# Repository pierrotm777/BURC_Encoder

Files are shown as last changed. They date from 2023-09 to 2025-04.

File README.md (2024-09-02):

# BURC_Encoder
 Universal RC Box System.  
 
 The BURC modules use the RCUL protocol by Rc-Navy.
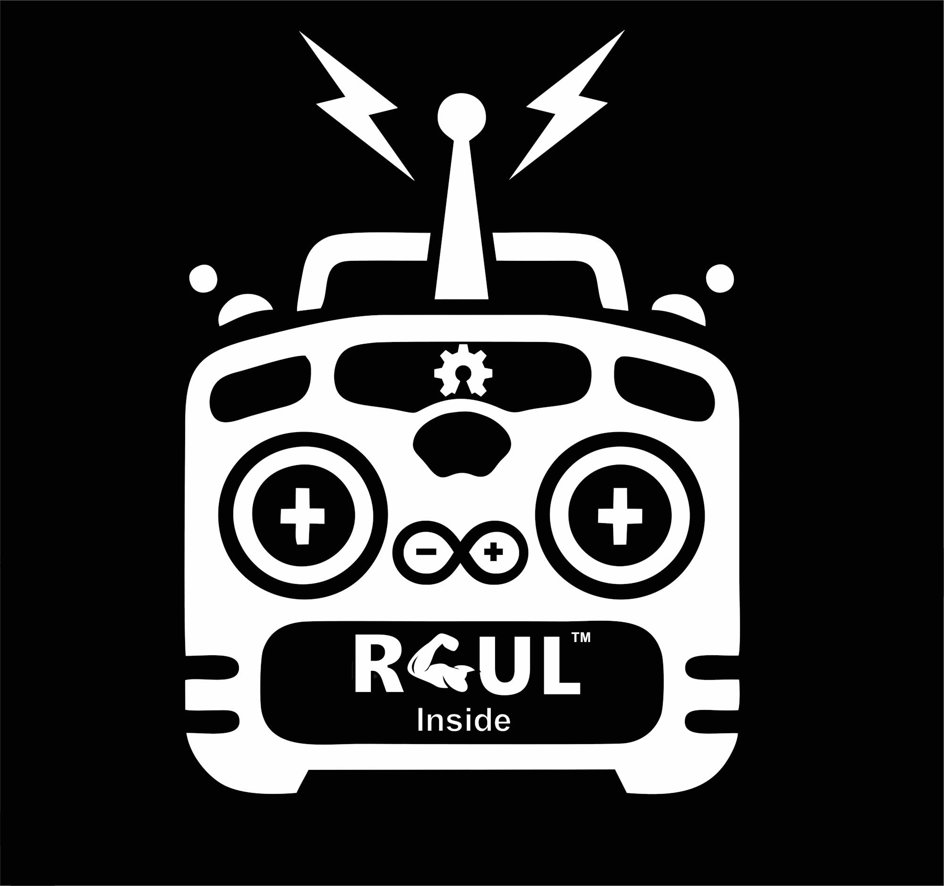
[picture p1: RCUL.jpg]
RCUL
   

## Rc-Navy
The BURC system is build by Philippe Loussouarn ([Rc-Navy](http://p.loussouarn.free.fr/index.html)). 

## Presentation of the BURC system
[What's BURC](https://p-loussouarn-free-fr.translate.goog/arduino/exemple/RCUL/RCUL.html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)

## Compatibles modules usable with BURC
All these modules behind
- [Ms8 v2](https://github.com/Ingwie/OpenAVRc_Hw/tree/V3/MutltiSwitch_Sw8_V2)  
- [Ms16](https://github.com/Ingwie/OpenAVRc_Hw/tree/V3/MultiSwitch_Sw16-ProMicro)  
- [Sound&SmokeModule](https://github.com/Ingwie/OpenAVRc_Hw/tree/V3/Sound%26SmokeModule)  
- [Xany2Msx](https://github.com/Ingwie/OpenAVRc_Hw/tree/V3/Xany2Msx/Firmware_Msx)  
- [Xany2Misc](https://github.com/Ingwie/OpenAVRc_Hw/tree/V3/Xany2Msx/Firmware_Misc)  
- Hall sensor:  
  * [Hall I2C sensor](https://github.com/Ingwie/OpenAVRc_Hw/tree/V3/Capteur_Hall_I2C)  
  * [Hall I2C sensor mini](https://github.com/Ingwie/OpenAVRc_Hw/tree/V3/Capteur_Hall_I2C_Mini)  
- [MultiSwitch_MosFet](https://github.com/Ingwie/OpenAVRc_Hw/tree/V3/MultiSwitch_MosFet)  
- [Ms8 Pulseq](https://github.com/Ingwie/OpenAVRc_Hw/tree/V3/PulseSeq) 
- [Servo 360°]() 

## Build BURC
### Schematic  
Encoder:  
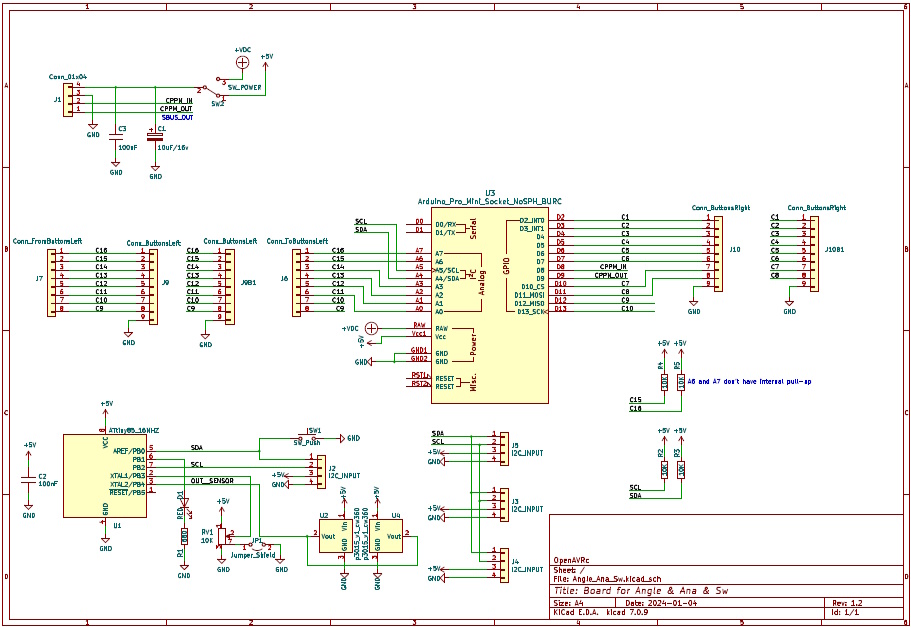
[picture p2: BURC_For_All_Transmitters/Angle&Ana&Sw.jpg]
Encoder
  
16 switchs by I2C bus:  
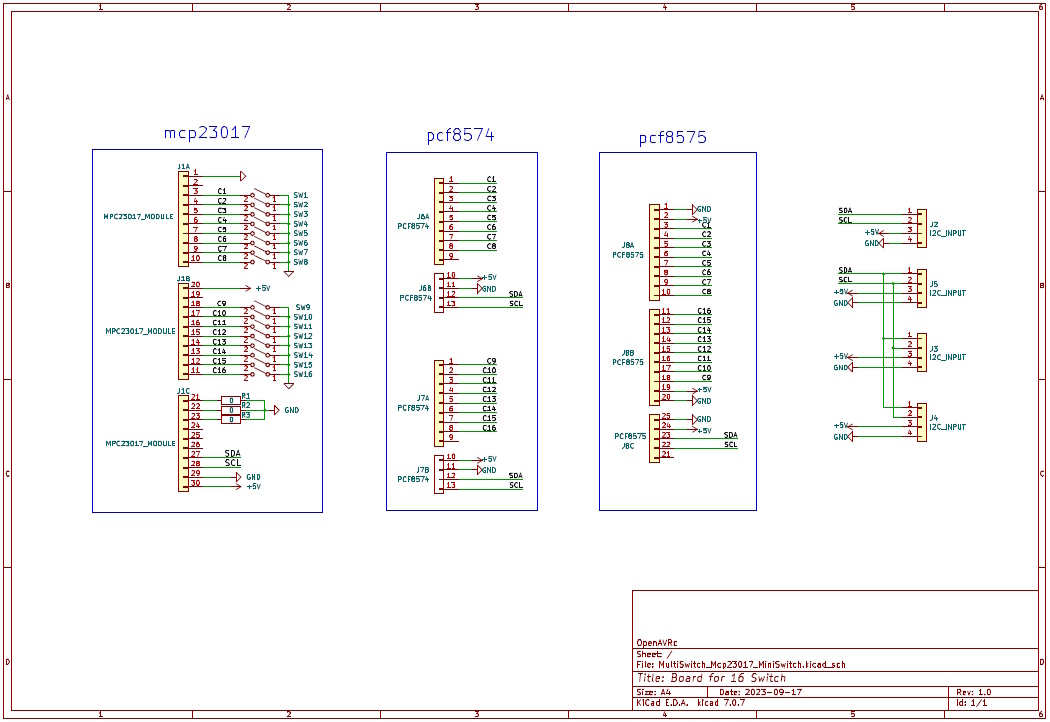
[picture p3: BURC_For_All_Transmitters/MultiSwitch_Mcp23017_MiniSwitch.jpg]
  
16 switchs on Arduino:  
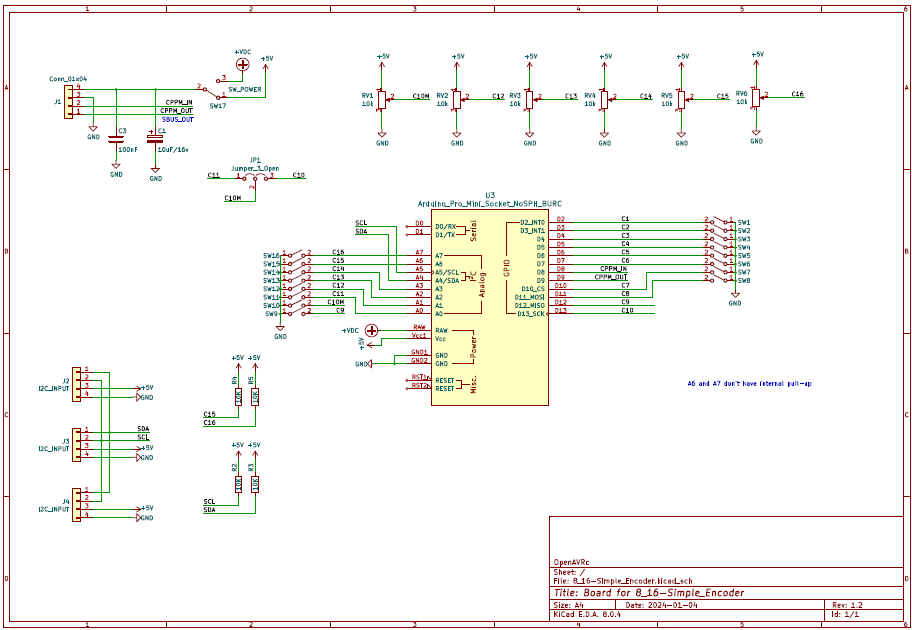
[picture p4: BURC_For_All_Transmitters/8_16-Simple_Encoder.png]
 

### Boards  
Two cards make up the BURC system.
The BURC Encoder is connected to the transmitter over a **CPPM** input or a **SBUS** input.
- The BURC Encoder:
  * Encoder board (include 8 switchs, 1 360° hall sensor and 1 slider, need one proportional channel) 
  Can command up to 128 fonctions (8x16) by exemple 8 Ms16 modules, use 1 channel for each 16 switchs module.  

  <table border="2">
  <tr>
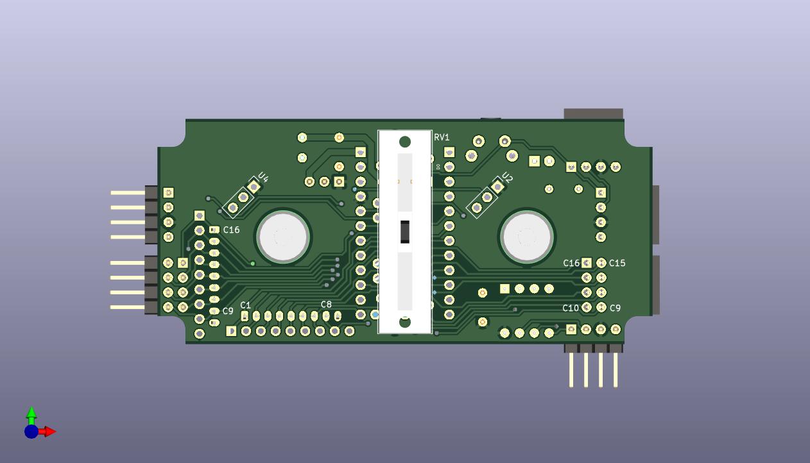
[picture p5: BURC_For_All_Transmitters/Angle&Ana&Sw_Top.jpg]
  <td></td>
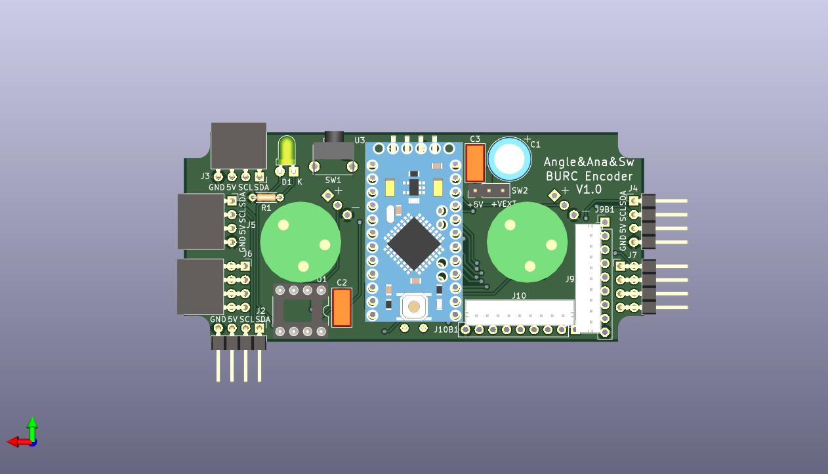
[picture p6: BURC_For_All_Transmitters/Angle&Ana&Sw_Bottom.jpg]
  <td></td>
  </tr>
  </table>
  
  The hall sensor command a Schottel motor type by rotation, and the slider command the motor's power.  
  This board is the **main board** system and can command **several 16 switchs** board.  
  The interface between all the boards use an **I2C** bus.  

  The same board can be used for the left or right motor, and assume to wire only one of the two hall sensor an the 8 first switchs.  
  The second board will command the 8 other switchs and the second slider (No need another arduino Pro Mini in the second circuit board) .  
  An Attiny85 receive these orders from the first board and command the second hall sensor and the second slider.  
  A dashboard exemple for two motors:  
  <table border="2">
  <tr>
  <td></td>
  </tr>
  </table>
    
  * Encoder symplified board (include 16 switchs or 8 switchs and 6 potentiometers, need one proportional channel) 
  Can command up to 128 fonctions (8x16) by exemple 8 Ms16 modules, use 1 channel for each 16 switchs module.  

  <table border="2">
  <tr>
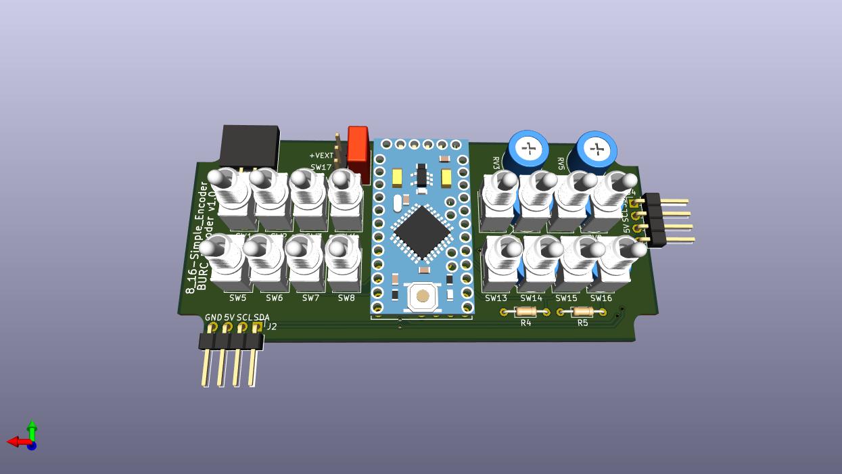
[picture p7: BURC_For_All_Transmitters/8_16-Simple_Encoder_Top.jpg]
  <td></td>
  </tr>
  </table>
  
  You need to remove the resistor's LED on pin D13 (C10 signal).  
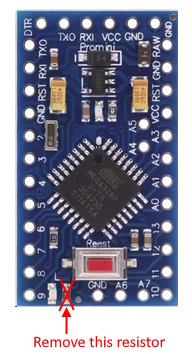
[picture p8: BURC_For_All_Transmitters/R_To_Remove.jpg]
R to remove
    

- The Switch board:

  16 Switchs board (need one proportional channel) 
  Each switch can command 1 fonction.  
  The type of command depend of the [Ms8](https://github.com/Ingwie/OpenAVRc_Hw/blob/V3/MutltiSwitch_Sw8_V2/MS8-Xany-V2_Manuel_Utilisateur.pdf)/[Ms16](https://github.com/Ingwie/OpenAVRc_Hw/blob/V3/MultiSwitch_Sw16-ProMicro/MS16-Xany_Manuel_Utilisateur.pdf) possibilities.    
  This board read 16 switchs by 1 MCP23017 or 2 PCF8574 or 1 PCF8575.
  <table border="2">
  <tr>
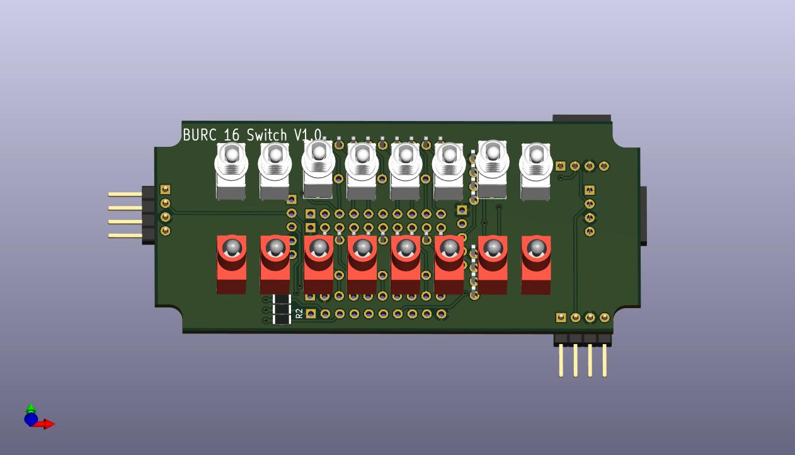
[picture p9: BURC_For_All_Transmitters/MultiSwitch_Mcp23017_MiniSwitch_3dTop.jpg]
  <td></td>
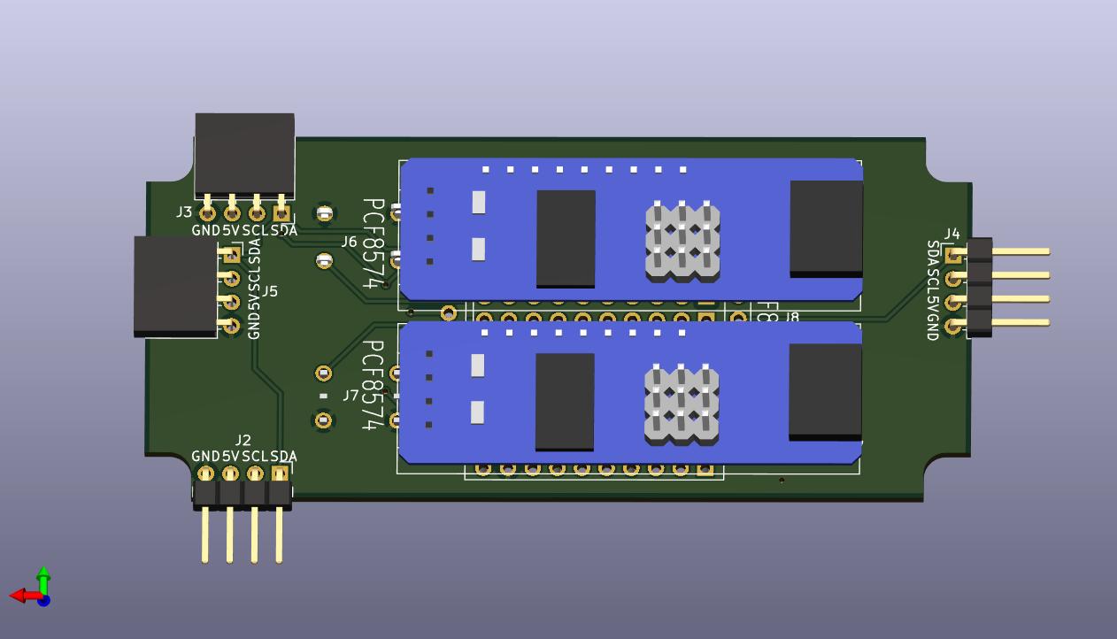
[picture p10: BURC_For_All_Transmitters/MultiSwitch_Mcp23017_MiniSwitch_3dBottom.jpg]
  <td></td>
  </tr>
  </table>  
  
  A main board coupled to  a second board and 2 16 switchs boards:
  <table border="2">
  <tr>
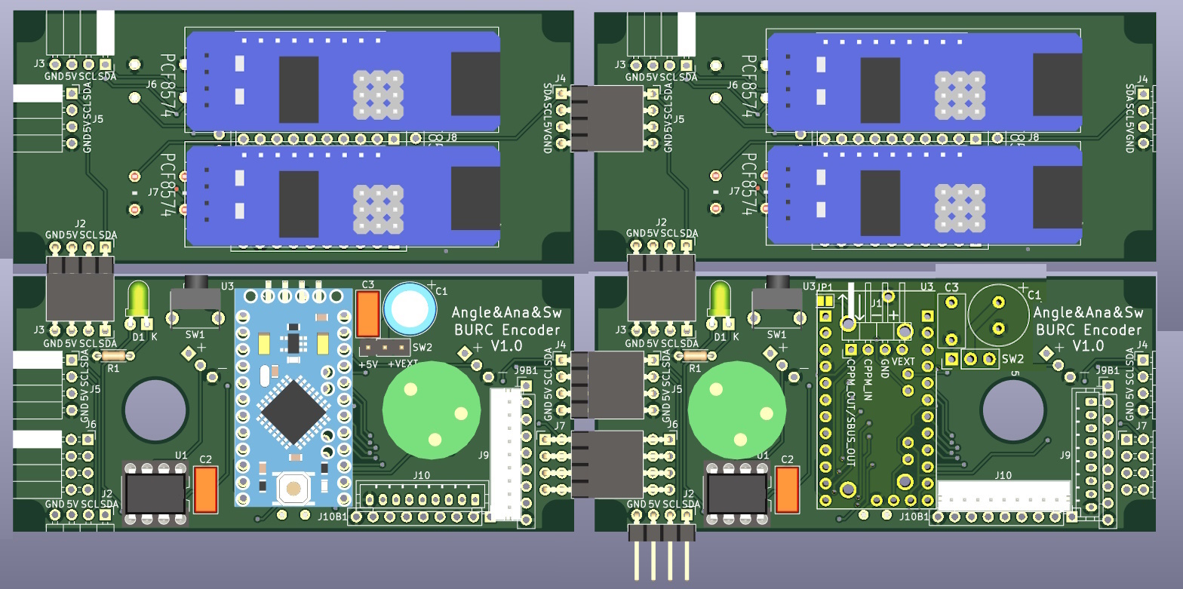
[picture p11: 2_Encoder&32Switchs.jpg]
  <td></td>
  </tr>
  </table>  
  
  A main board and a 48 switchs coupled:
  <table border="2">
  <tr>
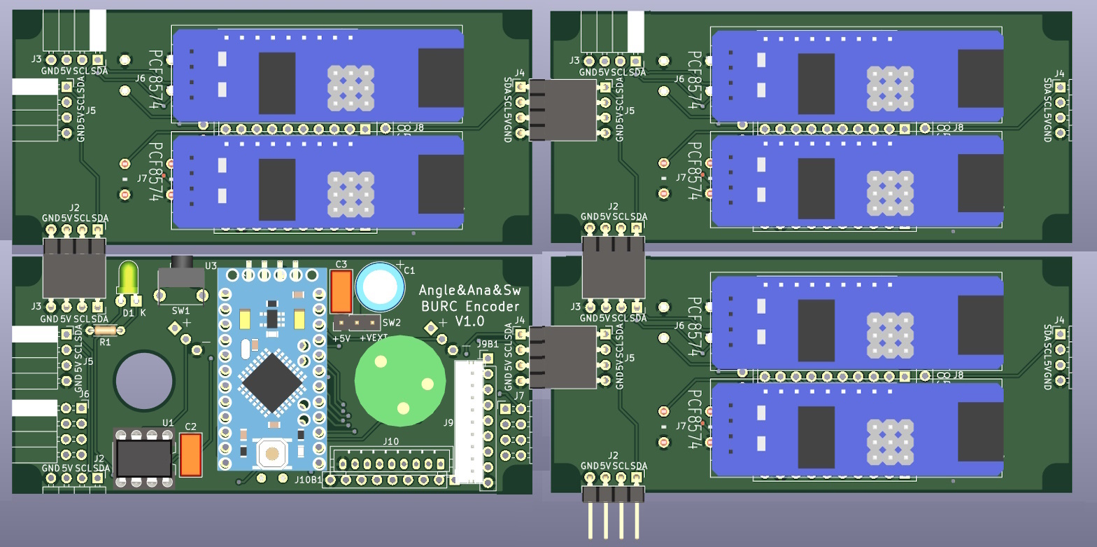
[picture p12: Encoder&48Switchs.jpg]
  <td></td>
  </tr>
  </table>  

### Firmware upload for Pro Mini
- Windows:  
The best method is to use [Xloader](https://github.com/pierrotm777/BURC_Encoder/blob/main/PROG/Windows/XLoader.zip).  
The last firmware is the version [v0.14](https://github.com/pierrotm777/BURC_Encoder/blob/main/PROG/Windows/BURC_CODER_V0_14.hex).  

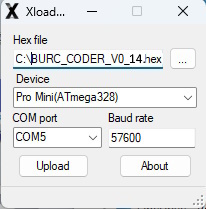
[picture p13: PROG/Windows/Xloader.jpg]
Xloader
  

- Other Os:
Use you Arduino IDE for find witch command to use.
In my case, the command is :  
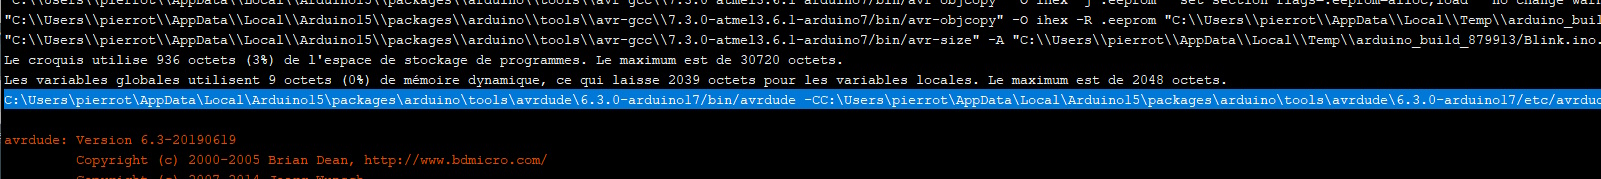
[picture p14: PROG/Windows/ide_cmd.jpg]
  
  * replace the hex file path C:\Users\pierrot\AppData\Local\Temp\arduino_build_879913/Blink.ino.hex by your firmware path.  
  * create a script file with this change.  

### Firmware upload for Attiny85
  * use an USBAsp programmer and [ARDUDESS Gui](https://github.com/ZakKemble/AVRDUDESS/releases/) or an [Arduino Uno board](https://www.instructables.com/Programming-ATtinys-Micro-Controllers-With-Arduino)
  * define the fuses (for 16Mhz internal mode), low=0xF1, high=0xDF, extended=0xFF
  * last firmware is the version [v2.2](https://github.com/pierrotm777/BURC_Encoder/blob/main/PROG/Windows/HallAna2A1335_V2_2.hex).  

### Exemple BURC build
- You will find [here](https://cults3d.com/fr/mod%C3%A8le-3d/jeu/burc-pad) an exemple of 3d files by **croky_b** witch accept all the BURC's boards.  

## Configure the BURC Encoder
  * Pro Mini:
    * Connect a FTDI interface to the Arduino Pro Mini and your PC.
    * Use a terminal for send your commands.
    * Set your terminal with 115200 bauds, 8 bits, no parity, 1 bit stop and CR or CRLF (see LIGNE.TERM).
    * Type ENTER key for see the module's version.

  * Attiny85 (360° encoder) A push button allows:
    * calibrating the analog sensor (min and max): before powering the ATtiny85, press the Push button and hold it for  1 - 2 seconds.
    * setting the I2C address: before powering the ATtiny85, press the Push button and hold it for more than 4 seconds.  
      Additionally, it can read an analogic input (0/5V)

## Settings usables
The list of messages that can be transported in each RCUL instance is:  
- SW1-SW8:   the state of 8 contacts of the 8 contacts of an 8 I/O I/O extender or a 16 I/O extender or the first 8 contacts of the 16 native contacts of the Arduino
- SW9-SW16:  the state of the last 8 contacts of a 16 I/O extender or the last 8 contacts of the 16 native contacts of the Arduino
- SW1-SW16:  the state of 16 contacts of a 16 I/O extender or of the 16 native contacts of the Arduino
- ANGLE:     the value of the angle of a 360° angle sensor
- ANGLE+ANA: the value of the angle of a 360° angular sensor + an analog value  

On the encoder there are 16 native contacts from C1 to C16.  
Among C8 to C16, 6 are also analog inputs which correspond to pins C11 to C16.  
So C11 to C16 are also ANA1 to ANA6 (these are my names, not the names of the "arduino" pins):  
We therefore have 6 analog channels at our disposal (just as we wire a pot there instead of an switch or push button).  

We can make extended RCUL messages of the type:  
**RCUL1.MESSAGE=C1-C8@0x00+ANA1** (which will transmit 8 contact states + an 8-bit ana value:  
You obviously have to wire a knob to pin C11).  
**RCUL2.MESSAGE=C9-C16@0x24+ANA2** (which will transmit 16 contact states + an 8-bit ana value:  
You obviously have to wire a knob to pin C12).  

So, with **RCUL1.MESSAGE=C1-C8@0x00+ANA1** or **RCUL2.MESSAGE=C9-C16@0x24+ANA2**,  
for an MS8 (V1 or V2), you can control the 8 outputs + the additional proportional output.  
You can also order the Sound&Smoke module which uses the 8 contacts to launch 8  
different sounds and the ana value to adjust the volume of the DF Player from the transmitter.  

We can also do:
**RCUL3.MESSAGE=C1-C16@0x25+ANA3** (which will transmit 16 contact states + an 8-bit analog value:  
You obviously have to wire a knob to pin C12)
So, with **RCUL3.MESSAGE=C1-C16@0x25+ANA3** for an MS16, you can control the 16 outputs + the additional proportional output.  

So, if we want to use the first 8 contacts C1 to C8 of your 16-input I2C extender at address 0x24,  
we just have to create another RCUL instance in which we refer to the first 8 contacts: **RCUL5.MESSAGE=C1-C8@0x24**
And with RCUL5 we can, for example, order another MS8.
So we will have the first 8 contacts of the I2C extender with 16 inputs (at address 0x24) used by RCUL5 to control an MS8 (for example) 
and the last 8 contacts of the 16-input I2C extender (at address 0x24) used by RCUL2 (which also uses ANA2) to control a Sound&Smoke.

It is possible to directly map an analog value (ANA1 to AN6), inverted or not, to a channel.  
To do this, you must use the command **RCULx.MESSAGE=RC.ANA[_INV]y** with x=RCUL instance number and y is the ANA channel number (from 1 to 6):  
Example: **RCUL4.MESSAGE=RC.ANA_INV1**  
A simple solution for build a little 6 channels hanset WITH BURC features.  

Debug method:  
To test an RCUL channel in CPPM, we loop pin8 back to pin9 and we do an **RX.MODE=RCUL4@CPPM4** and after an **RX.DBG=1** command.  

## I2C Devices address
<pre>
PCF8574         <b>0x20 to 0x23</b>  
MCP23017        <b>0x24 to 0x27</b>  
PCF8574A        <b>0x38 to 0x3B</b> (very difficult to find)  
PCF8575         <b>0x24 to 0x27</b>  
PCF8575A        <b>0x3C to 0x3F</b> (very difficult to find)  
ANGLE SENSOR    <b>0x0C to 0x0F</b>  
</pre>

Exemple of configuration:
```
CONF?
LANG=FR
LIGNE.TERM=CRLF
ECOLAGE.MODE=CPPM_OUT
CPPM.MODU=NEG
CPPM.ENTETE=300
CPPM.VOIE.NB=8
CPPM.PERIODE=22500
RCUL.REPET=2
RCUL1.VOIE=5
RCUL1.MESSAGE=ANGLE+ANA@0x0C
RCUL1.TEST=OFF
RCUL2.VOIE=6
RCUL2.MESSAGE=C9-C16@0x24
RCUL2.TEST=OFF
RCUL3.VOIE=8
RCUL3.MESSAGE=C1-C8@0x24+ANA1
RCUL3.TEST=OFF
RCUL4.VOIE=7
RCUL4.MESSAGE=RC.ANA_INV1
RCUL4.TEST=OFF
RCUL5.VOIE=OFF
RCUL5.MESSAGE=C1-C8@0x00
RCUL5.TEST=OFF
RCUL6.VOIE=OFF
RCUL6.MESSAGE=C1-C8@0x00
RCUL6.TEST=OFF
RX.MODE=RCUL6@CPPM6
RX.DBG=0
```

<pre>
- LANG=FR                       define language (FR or UK)  
- LIGNE.TERM=CRLF               define terminal return (CR or CRLF)  
- ECOLAGE.MODE=CPPM_OUT         CPPM_OUT+CPPM_IN/CPPM_OUT/SBUS_OUT;FUTABA[_INV] Defines the transmitter training mode
- CPPM.MODU=NEG                 CPPM signal is build with negative pulses (POS is possible)  
- CPPM.ENTETE=300               300 first width CPPM pulse  
- CPPM.VOIE.NB=8                CPPM build 8 channels  
- CPPM.PERIODE=22500            CPPM periode in mS
- SBUS.SPEED=NORMAL				NORMAL/FAST Defines the SBUS speed (NORMAL=14ms, FAST=7ms)  
- RCUL.REPET=2                  the encoder repeats the same thing twice for a better transmission result  
- RCUL1.MESSAGE=ANGLE+ANA@0x0C  for command an azimutal motor (direction and motor)  
- RCUL2.MESSAGE=C9-C16@0x24     8 buttons on MCP23017 (address 0x24)  
- RCUL3.MESSAGE=C1-C8@0x24+ANA1 8 buttons on MCP23017 and analog button (module Sound&Smoke for 8 sounds et volume)
- RCUL4.MESSAGE=RC.ANA_INV2     1 analogique channel inverted  
</pre>

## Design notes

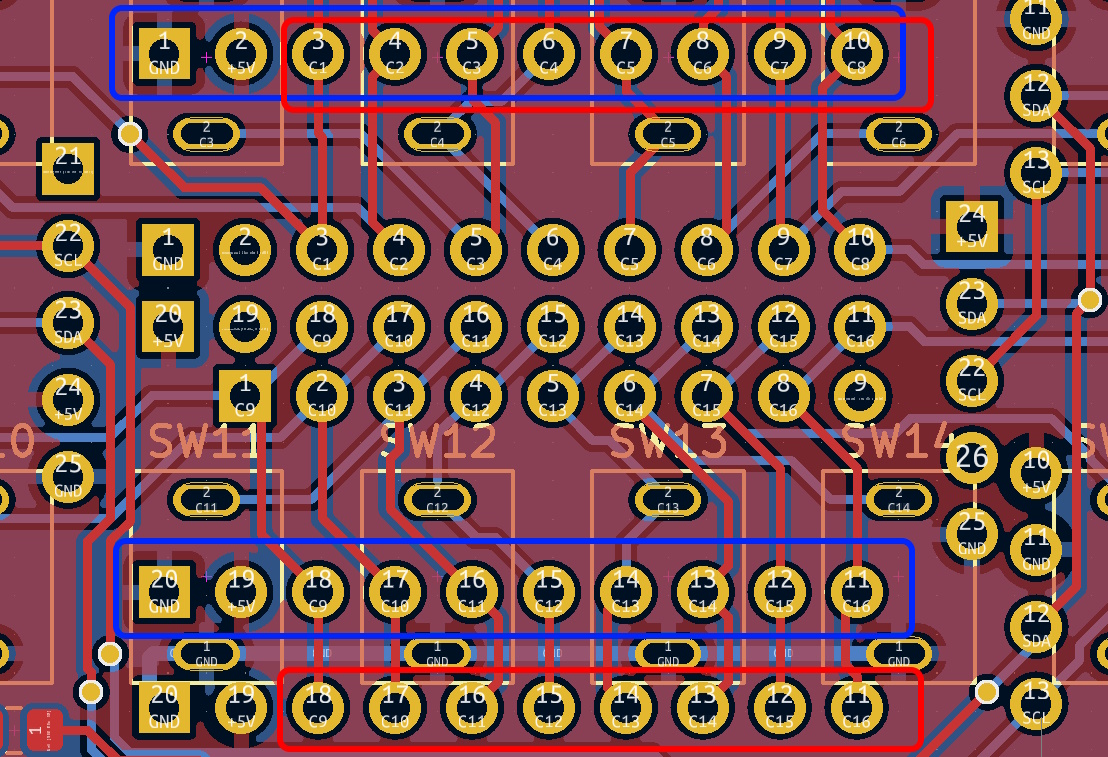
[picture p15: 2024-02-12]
BURC_For_All_Transmitters/PCF8575_pinout.jpg

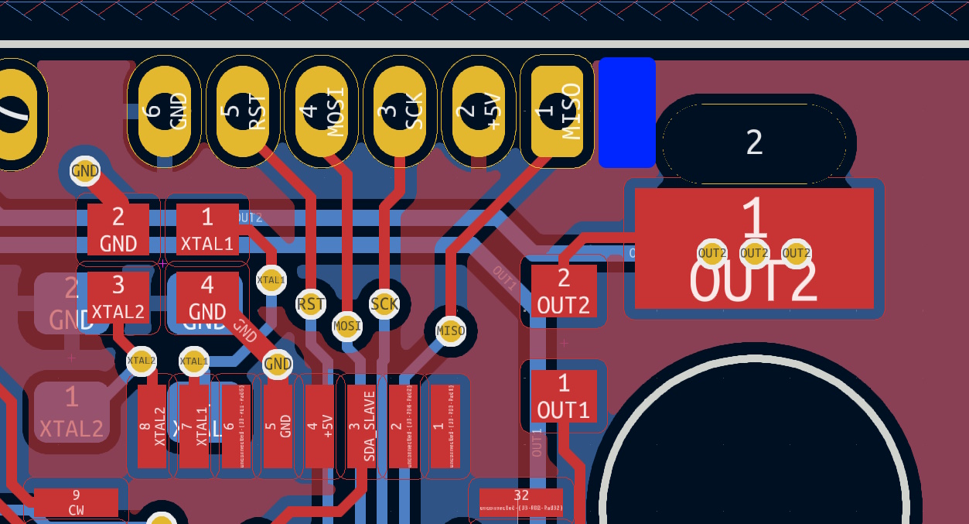
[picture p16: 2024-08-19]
ESC.jpg

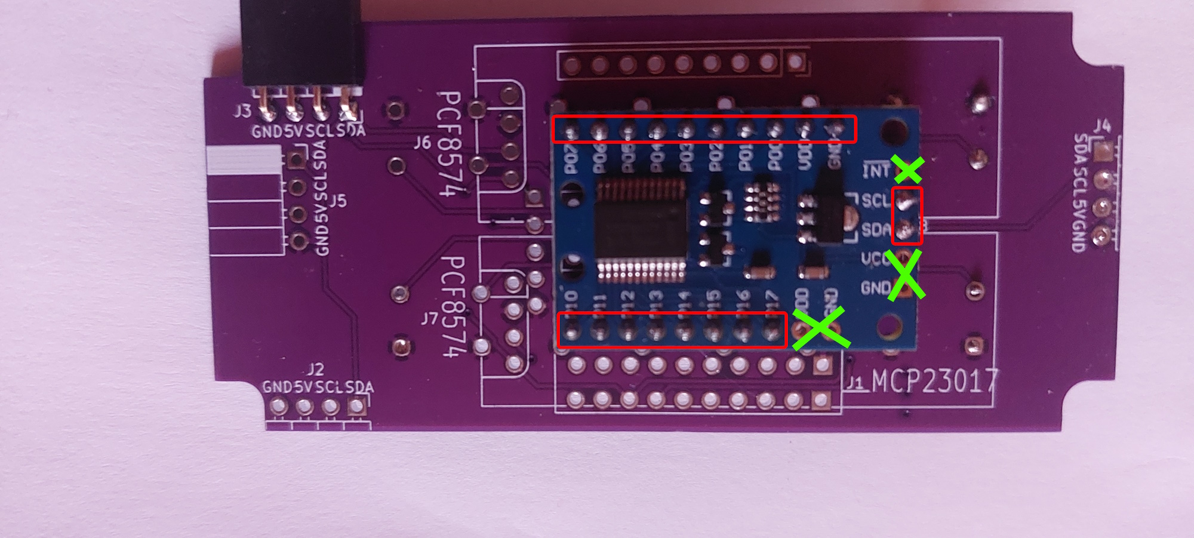
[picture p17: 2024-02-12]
BURC_For_All_Transmitters/pcf8575_bleu.jpg

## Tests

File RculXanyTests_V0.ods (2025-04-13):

REGLAGES ENSEMBLE CODEUR/DECODEUR BURC POUR DIFFERENTS EMETTEURS/RECEPTEURS
Codeur BURC |  |  | Emetteur |  |  | Récepteur |  | Décodeur BURC
Modèle | Mode | Répétition(s) | Entrée Ecolage | Modèle | Voie -/+ % | Modèle | Interface de Sortie | Modèle | Niveau Filtrage
BURC | CPPM 8 Voies T=22ms | 2 | CPPM | Radiomaster TX16S | 100 | FrSky X8R | PWM | XanySpyV7 | 0
BURC | CPPM 8 Voies T=22ms | 2 | CPPM | Radiomaster TX16S | 100 | FrSky X8R | SBUS | XanySpyV7 | 0
BURC | SBUS Normal | 2 | SBUS | Radiomaster TX16S | 100 | FrSky X8R | PWM | XanySpyV7 | 0
BURC | SBUS Normal | 2 | SBUS | Radiomaster TX16S | 100 | FrSky X8R | SBUS | XanySpyV7 | 0
BURC | SBUS Normal | 2 | SBUS | Radiomaster TX16S | 100 | FlySky FS-IA10B | PWM | XanySpyV7 | 2
BURC | SBUS Normal | 2 | SBUS | Radiomaster TX16S | 100 | FlySky FS-IA10B | IBUS | XanySpyV7 | 2
BURC | SBUS Normal | 2 | SBUS | Radiomaster TX16S | 100 | FlySky FS-IA10B | SBUS | XanySpyV7 | 2
BURC | SBUS Normal | 2 | SBUS | Radiomaster TX16S | 100 | FlySky FS-IA10B | CPPM | XanySpyV7 | 2
BURC | SBUS Normal | 1 | SBUS | Radiomaster TX16S | 100 | Graupner GR-12L | PWM | XanySpyV7 | 0
BURC | SBUS Normal | 1 | SBUS | Radiomaster TX16S | 100 | Graupner GR-24 Pro +3xG +3A + 3M + Vario | SUMD | XanySpyV7 | 0
BURC | SBUS Normal | 1 | SBUS | Radiomaster TX16S | 132 | Hitec Optima 7 | PWM | XanySpyV7 | 0
BURC | SBUS Normal | 1 | SBUS | Radiomaster TX16S | 132 | Spektrum ART6610T | PWM | XanySpyV7 | 0
BURC | SBUS Normal | 4 | SBUS | Radiomaster TX16S | 88 | Multiplex RX—9-DR SRXL16 | PWM | XanySpyV7 | 3

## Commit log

2023-09-07 Create BURC system repo JR and Other
    [200AWMSP1T2A1M2RE.stp, 22-17-2057.stl, 6mm SPDT Mini Toggle Switch.step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]
2023-09-07 Add schematics
2023-09-11 Swap CPPM_IN/CPPM_OUT
    [Angle&Ana&Sw-B_Adhesive.gbr, Angle&Ana&Sw-B_Cu.gbr, Angle&Ana&Sw-B_Fab.gbr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]
2023-09-17 Update schematic switch board
    [MultiSwitch_Mcp23017_MiniSwitch.kicad_sch]
2023-10-01 Update
    Corrections diverses:
    - perçages bouton reset, potentiomètre linéaire.
    - ajout pullup i2c
    [Angle&Ana&Sw-B_Adhesive.gbr, Angle&Ana&Sw-B_Cu.gbr, Angle&Ana&Sw-F_Adhesive.gbr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]
2023-10-01 Update drill switch
    [MultiSwitch_Mcp23017_MiniSwitch-B_Adhesive.gbr, MultiSwitch_Mcp23017_MiniSwitch-B_Cu.gbr, MultiSwitch_Mcp23017_MiniSwitch-B_Fab.gbr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]
2024-01-04 remove files
    [22-17-2057.stl, Arduino Pro Mini v7.step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]
2024-01-04 Compression fichiers et ajout fichiers fab
    [200AWMSP1T2A1M2RE.stp, 6mm SPDT Mini Toggle Switch.step, Angle&Ana&Sw.kicad_pcb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]
2024-01-04 Update gerber
2024-01-04 remove gerber into zip files
2024-02-12 Update Multiswitch board
    Remove several pads for the pcf8575 option
2024-07-23 add schematic
2024-07-24 add fuses attiny85 infos
2024-07-27 Add 8-16 switchs gerber board files
2024-07-27 add 8_16-Simple_Encoder schematic
2024-08-19 add remove resistor detail
2025-04-13 update firmware code
    [RculXanyTests_V0.ods]
